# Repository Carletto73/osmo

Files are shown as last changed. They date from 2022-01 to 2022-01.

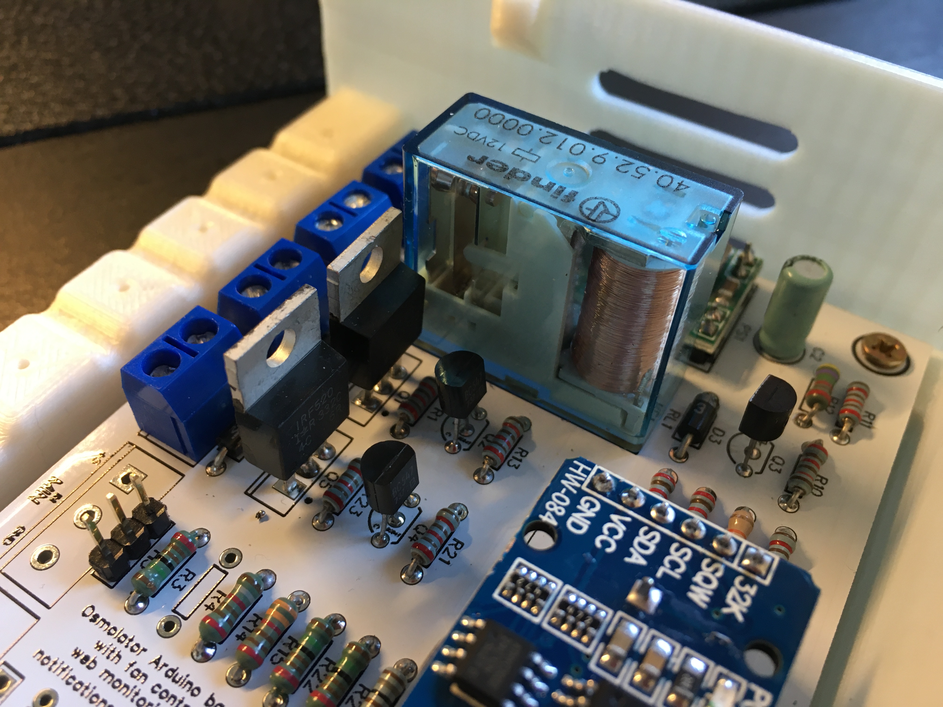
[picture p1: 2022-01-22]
assembly/IMG_1388.JPG

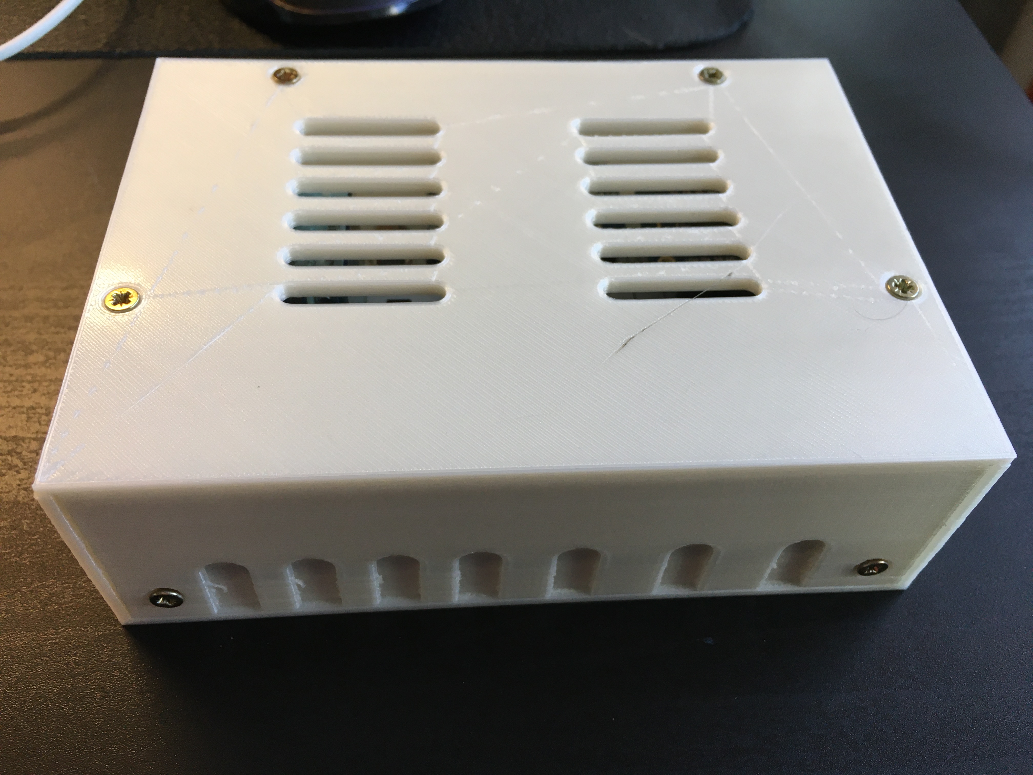
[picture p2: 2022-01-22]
assembly/IMG_1394.JPG

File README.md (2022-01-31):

# osmo
Osmolator for aquarium Arduino based



The typical osmolators are just a simple relay that feed the pump when the water level in the tank is low. This osmolator add several feature like:
1) web server to check the hystory of the pump activation
2) Telegram interface for settings and alarms
3) pump softstart and softstop
4) diagnostic of MIN and MAX level sensors
5) auto-diagnostic of power stadium inside the devise
6) temperature sensors and FAN output in case of water too hot







Web server for parametrization, status check, network credential change, ...



Telegram robot to check the osmolator status



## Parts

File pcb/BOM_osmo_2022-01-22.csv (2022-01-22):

ID | Name | Designator | Footprint | Quantity | Manufacturer Part | Manufacturer | Supplier | Supplier Part | Price
1 | M035MM | AUX,AUX,DS18B20,DS18B20,MIN,MIN | SCREWTERMINAL-5MM-3 | 6
2 | 100uF | C1,C1 | CAP_TH_6.3MM | 2
3 | 22uF | C2,C2,C3,C3 | CAP_TH_5MM | 4
4 | 1N4007 | D1,D2,D3,D4 | DO-41_BD2.4-L4.7-P8.70-D0.9-FD | 4 | 1N4007 | Yangzhou Yangjie Elec Tech | LCSC | C211605 | 0.025
5 | EM513 | D1,D2,D3,D4 | DO-41_BD2.4-L4.7-P8.70-D0.9-FD | 4 | 1N4007 | Yangzhou Yangjie Elec Tech | LCSC | C211605 | 0.025
6 | HDR1X5-M | EXP,EXP | HDR-TH_5P-P2.54-V-M | 2 | HDR1X5-M | null | LCSC | C9900001260
7 | M025MM | FAN,FAN,MAX,MAX,PUMP,PUMP,VIN,VIN | SCREWTERMINAL-5MM-2 | 8
8 | Header-Male-2.54_1x3 | H1,H1,H2,H2,H3,H3,H4,H4 | HDR-TH_3P-P2.54-V-M-1 | 8 | Header2.54mm 1*3P | BOOMELE | LCSC | C49257 | 0.017
9 | MP1584EN MODULE | PS1,PS1 | MP1584EN-MODULE | 2 | MP1584EN Module
10 | IRF540 | Q1,Q1,Q5,Q5 | TO-220-3_L10.0-W4.5-P2.54-L | 4 | IRF540ZP | VBsemi Elec | LCSC | C709597 | 1.149
11 | BC547 | Q2,Q2,Q4,Q4 | BC547B 01 [PCB] | 4 | BC547 | SHIVRAM | SHIVRAM | BC547
12 | 2N2222A | Q3,Q3 | NPN-2N2222A | 2 | 2N2222A | Mauser | LCSC | C358533 | 0.032
13 | 10k | R1,R5,R6,R7,R10,R11,R13,R21,R23 | R_AXIAL-0.3 | 9
14 | 12k | R1,R5,R6,R7,R10,R11,R13,R21,R23 | R_AXIAL-0.3 | 9
15 | 1k | R2,R3,R4,R9,R14,R17,R17,R18,R18,R19,R19,R22 | R_AXIAL-0.3 | 12
16 | 1k5 | R2,R3,R14,R22 | R_AXIAL-0.3 | 4
17 | not mount | R4 | R_AXIAL-0.3 | 1
18 | 47k | R8,R12,R12 | R_AXIAL-0.3 | 3
19 | 68k | R8 | R_AXIAL-0.3 | 1
20 | 1k8 | R9 | R_AXIAL-0.3 | 1
21 | 3k3 | R15,R15,R16,R16 | R_AXIAL-0.3 | 4
22 | 4k7 | R20,R20 | R_AXIAL-0.3 | 2
23 | 40.52.9.012.0000 | RL1,RL1 | FINDER-40.52 | 2 | New SchematicLib
24 | WEMOS_D1_MINI_PRO | U1,U1 | DIP-16_WEMOS_D1_MINI_PRO4 | 2 | Wemos_D1_mini_Pro4 | null | LCSC | C2837266
25 | RTC-DS3231-AT24C32 | U2,U2 | RTC-DS3231-AT24C32 | 2

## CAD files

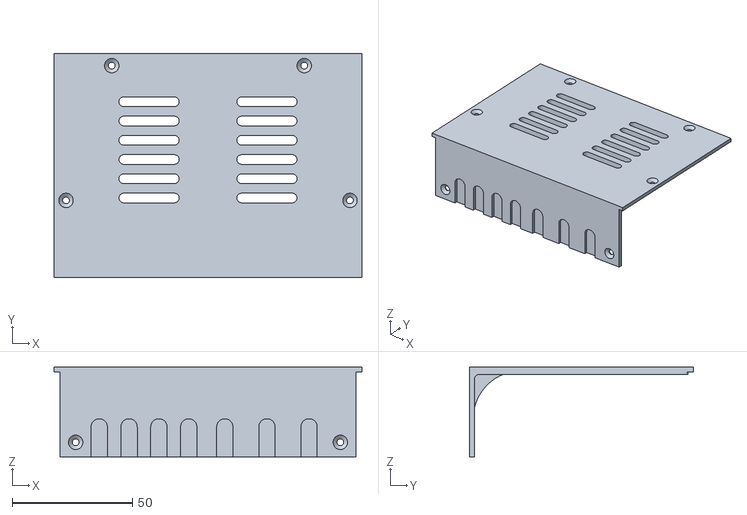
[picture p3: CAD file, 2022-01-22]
box/osmo_cover.stl
128.0 x 93.0 x 37.2

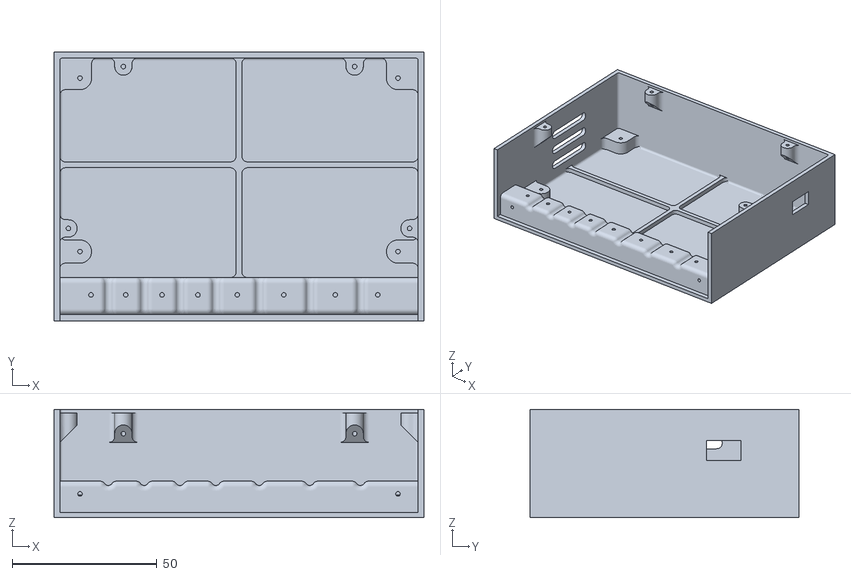
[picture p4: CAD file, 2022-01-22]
box/osmo_base.stl
128.0 x 93.0 x 37.4

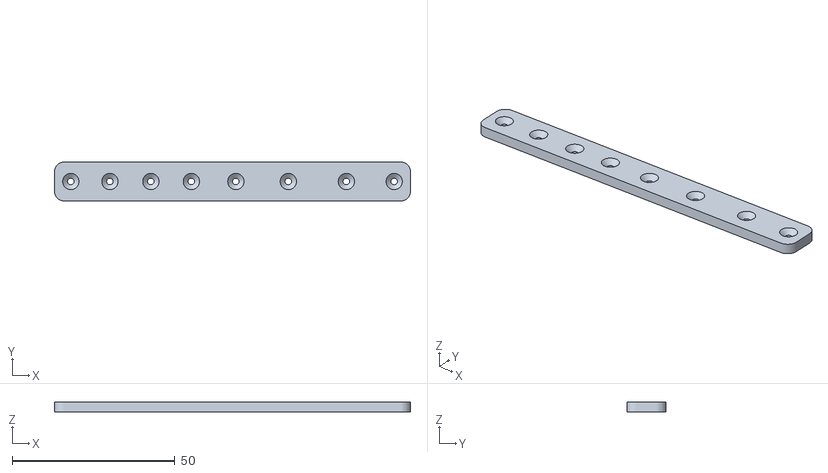
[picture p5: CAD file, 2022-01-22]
box/osmo_tpu.stl
109.2 x 12.0 x 3.00

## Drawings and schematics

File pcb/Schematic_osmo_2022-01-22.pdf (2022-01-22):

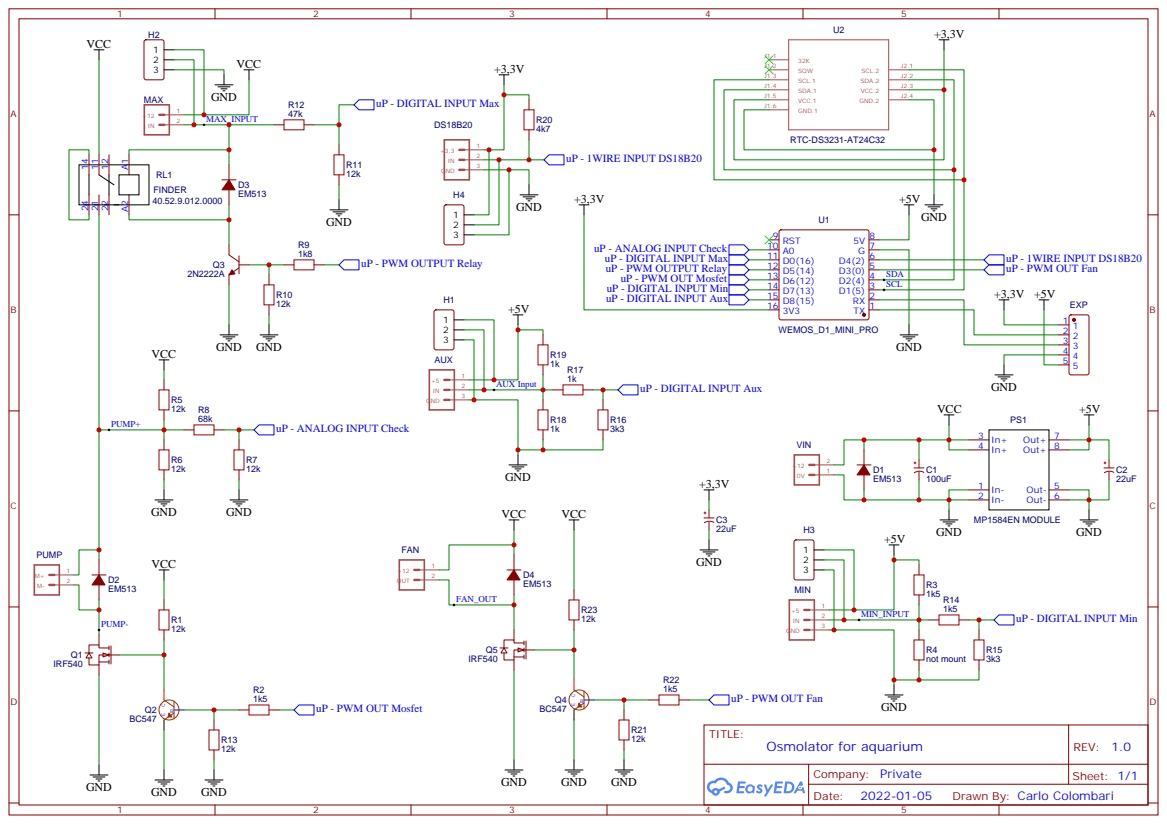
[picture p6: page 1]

uP - ANALOG INPUT Check
uP - DIGITAL INPUT Max
uP - PWM OUTPUT Relay
uP - PWM OUT Mosfet
uP - DIGITAL INPUT Min
uP - DIGITAL INPUT Aux

uP - 1WIRE INPUT DS18B20
uP - PWM OUT Fan

Drawn By: Carlo Colombari

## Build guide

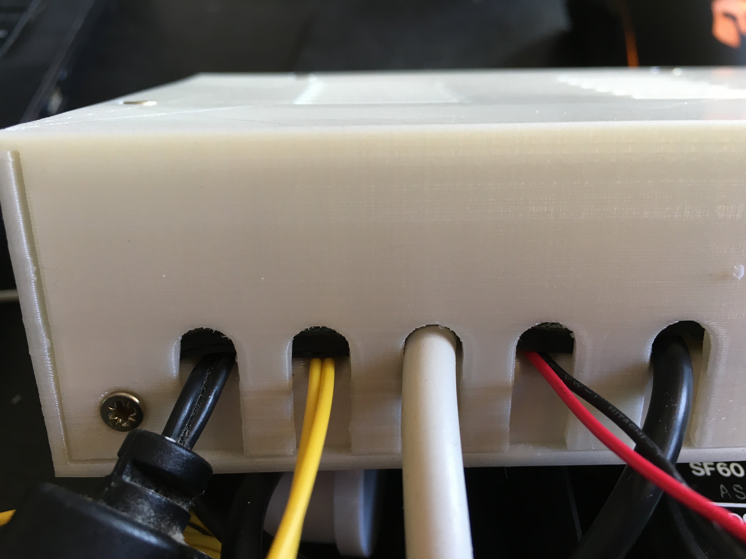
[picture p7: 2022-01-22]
assembly/IMG_1399.JPG

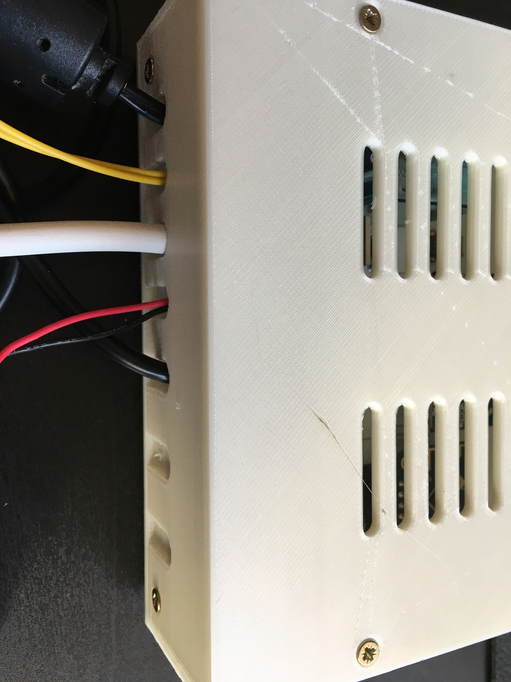
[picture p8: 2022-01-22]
assembly/IMG_1400.JPG

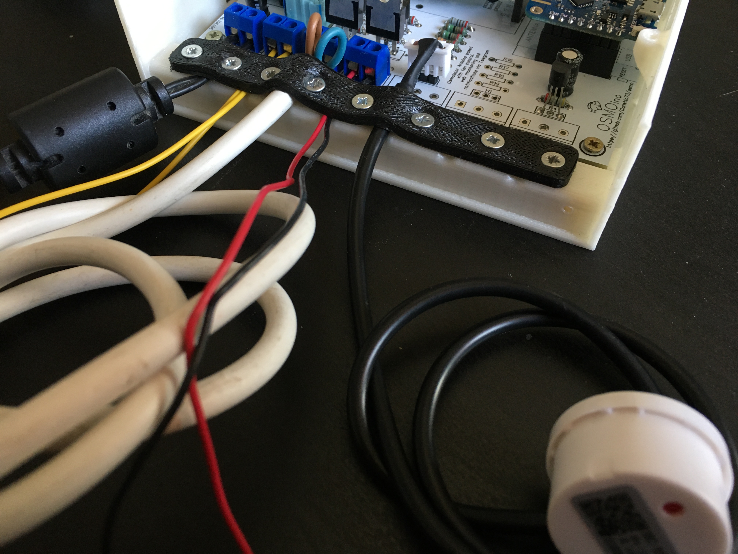
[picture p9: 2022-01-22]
assembly/IMG_1397.JPG

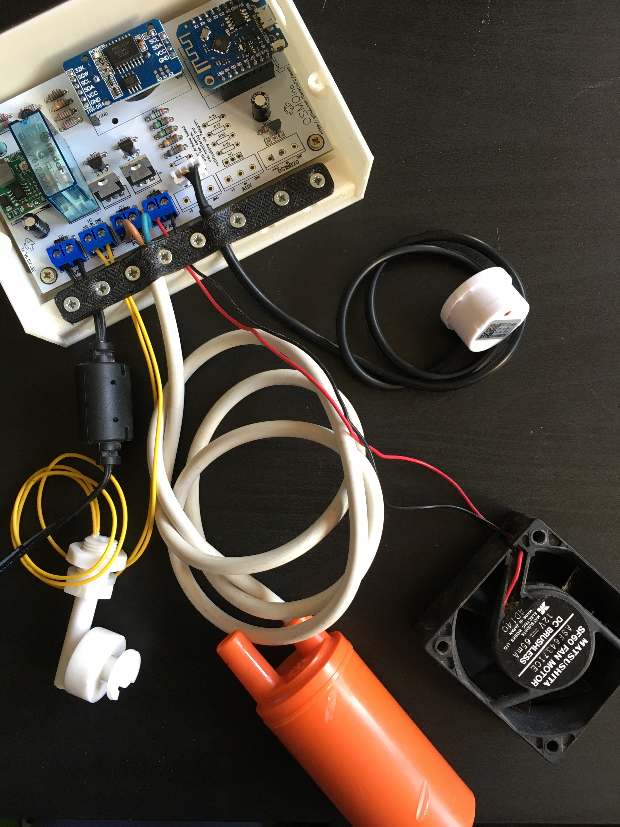
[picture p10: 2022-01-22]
assembly/IMG_1395.JPG

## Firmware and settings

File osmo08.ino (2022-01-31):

/*
  release 08: release candidate
*/

#include <ESP8266WiFi.h>
#include <WiFiClient.h>
#include <ESP8266WebServer.h>
#include <ESP8266mDNS.h>
#include <EEPROM.h>
#include <Arduino.h>
#include "AsyncTelegram.h"
#include <microDS3231.h>
#include <OneWire.h>
#include <DS18B20.h>
#include <AT24Cxx.h>

// EEPROM inside the DS3231 initialization
#define i2c_address 0x57
AT24Cxx eep(i2c_address, 32);

// OneWire and DS18B20 initialization
#define ONE_WIRE_BUS              2
OneWire oneWire(ONE_WIRE_BUS);
DS18B20 sensor(&oneWire);

// Created object for Telegram
AsyncTelegram myBot;

// Created object for RTC
MicroDS3231 rtc;

// Declaration
byte test;
byte state_releveling = 0;
byte pwm_pump = 255;
byte pwm_fan = 255;
byte pump_fault = 0;
byte last_second_start = 0;
byte last_minute_start = 0;
byte last_hour_start = 0;
byte last_day_start = 0;
byte last_month_start = 0;
byte last_year_start = 0;
byte last_dev_temperature_start = 0;
byte param_filt_max_level = 0;
byte param_filt_min_level = 0;
float param_temp_fan_activation = 0;
byte param_fan_hysteresis = 0; 
byte param_max_time_pump_on = 60;

int signal_percent[] = {0, 0, 0, 0, 0, 0, 4, 6, 8, 11, 13, 15, 17, 19, 21, 23, 26, 28, 30, 32, 34, 35, 37, 39, 41, 43, 45, 46, 48, 50, 52, 53, 55, 56, 58, 59, 61, 62, 64, 65, 67, 68, 69, 71, 72, 73, 75, 76, 77, 78, 79, 80, 81, 82, 83, 84, 85, 86, 87, 88, 89, 90, 90, 91, 92, 93, 93, 94, 95, 95, 96, 96, 97, 97, 98, 98, 99, 99, 99, 100, 100, 100, 100, 100, 100, 100, 100, 100, 100, 100, 100, 100, 100, 100, 100, 100, 100, 100, 100, 100};
String st;
float temperature_water;
unsigned long prev_overflow_time;
unsigned long prev_minimum_level_time;
unsigned long begin_time_timeout_pump;
unsigned long prev_state_releveling_time;
unsigned long prev_time_with_pump_stopped;
unsigned long duration_last_pumping;
bool water_overflow = true;
bool water_under_limit = false;
bool mosfet_closed = false;
bool relay_closed = false;
bool pump_timeout = false;
bool pump_stopped_in_previus_activation = true;
bool rtc_working = false;
bool pumping_ended_in_overflow = false;
bool telegram_unconnected;
bool connection_timeout;
bool request_change_account;
bool request_history;
bool request_parameter;
bool fan_switched_on = false;
bool request_preset_available = false;    

// E²PROM
// 0÷95 ID & PSW router
// 96÷159 Token telegram
// 160 pump_fault
// 161 param_filt_max_level
// 162 param_filt_min_level
// 163 param_temp_fan_activation (not float but 24°C + (value 163 * 0.1°C) )
// 164 param_fan_hysteresis
// 165 param_max_time_pump_on

#define OUTPUT_RELAY 14
#define OUTPUT_MOSFET 12
#define OUTPUT_FAN 0
#define ANALOG_INPUT_CHECK A0
#define INPUT_MAX_LEVEL 16
#define INPUT_MIN_LEVEL 13

// Create an instance of the server
// specify the port to listen on as an argument
ESP8266WebServer server(80);

// Main routine
void pump_manager()
{
  unsigned long current_time = millis();

  //Request if the temperature reading is available and launch a new reading
  if (sensor.isConversionComplete())
  {
    temperature_water = sensor.getTempC();  
    sensor.requestTemperatures();
  }

  // Filter on MAX level input
  if (digitalRead(INPUT_MAX_LEVEL))
  {
    if (current_time > (prev_overflow_time + (param_filt_max_level * 100))) // filter for max level
    {
      water_overflow = false;
    }
  }
  else
  {
    prev_overflow_time = current_time;
    water_overflow = true;
  }

  // Filter on MIN level input
  if (digitalRead(INPUT_MIN_LEVEL))
  {
    if (current_time > (prev_minimum_level_time + (param_filt_min_level * 100))) // filter for min level
    {
      water_under_limit = true;
    }
  }
  else
  {
    prev_minimum_level_time = current_time;
    water_under_limit = false;
  }

// These value are taken experimentally
  if (analogRead(ANALOG_INPUT_CHECK) < 175)
  {
    mosfet_closed = true;
    relay_closed = false;
  }
  else if (analogRead(ANALOG_INPUT_CHECK) > 525)
  {
    mosfet_closed = false;
    relay_closed = true;
  }
  else
  {
    mosfet_closed = false;
    relay_closed = false;
  }
  
// If is all right start the routine that feed check the hardware and starts the motor
  if(water_under_limit && !water_overflow && !pump_fault && pump_stopped_in_previus_activation)
  {
    switch (state_releveling)
    {
      case 0: // begin of pump phase
        if (rtc_working)
        {
          last_second_start = rtc.getSeconds();
          last_minute_start = rtc.getMinutes();
          last_hour_start = rtc.getHours();
          last_day_start = rtc.getDate();
          last_month_start = rtc.getMonth();
          last_year_start = rtc.getYear() % 100;
          last_dev_temperature_start = rtc.getTemperature();
          //stringHTML += String(rtc.getTemperatureFloat()).substring(0, 4);
        }
        else
        {
          last_second_start = 0;
          last_minute_start = 0;
          last_hour_start = 0;
          last_day_start = 1;
          last_month_start = 1;
          last_year_start = 20;
          last_dev_temperature_start = 0;
        }
        state_releveling = 1;
        prev_state_releveling_time = current_time;
        duration_last_pumping = 0;
        pumping_ended_in_overflow = false;
        break;
      case 1: // check if mosfet and relay are open
        if (current_time > (prev_state_releveling_time + 100))
        {
          prev_state_releveling_time = current_time;
          if (!mosfet_closed && !relay_closed)
          {
            state_releveling = 2;
          }
          else
          {
            if (relay_closed) 
            {
              pump_fault = 1;  // pump_fault = 1 >>> Relay stucked 
              EEPROM.write(160, pump_fault);
              EEPROM.commit();
            }
            if (mosfet_closed)
            {
              pump_fault = 2; // pump_fault = 2 >>> Mosfet in short-circuit
              EEPROM.write(160, pump_fault);
              EEPROM.commit();
            }
          }
        }
        break;
      case 2: // check if the mosfet works
        analogWrite(OUTPUT_MOSFET, 0); // Switch ON the mosfet
        if (current_time > (prev_state_releveling_time + 100))
        {
          prev_state_releveling_time = current_time;
          if (mosfet_closed)
          {
            analogWrite(OUTPUT_MOSFET, 255); // Switch OFF the mosfet
            state_releveling = 3;
          }
          else
          {
            pump_fault = 3; // pump_fault = 3 >>> Mosfet don't work
            EEPROM.write(160, pump_fault);
            EEPROM.commit();
          }
        }
        break;
      case 3: // delay
        if (current_time > (prev_state_releveling_time + 100))
        {
          prev_state_releveling_time = current_time;
          state_releveling = 4;
        }
        break;
      case 4: // check if the relay works
        digitalWrite(OUTPUT_RELAY, HIGH);
        if (current_time > (prev_state_releveling_time + 100))
        {
          prev_state_releveling_time = current_time;
          if (relay_closed)
          {
            state_releveling = 5;
          }
          else
          {
            pump_fault = 4; // pump_fault = 4 >>> Relay don't work
            EEPROM.write(160, pump_fault);
            EEPROM.commit();
          }
        }
        break;
      case 5: // soft-start pump
        prev_state_releveling_time = current_time;
        if (pwm_pump > 0)
        {
          pwm_pump--;
        }
        else
        {
          state_releveling = 6;
          begin_time_timeout_pump = current_time;
        }
        analogWrite(OUTPUT_MOSFET, pwm_pump); // 0=Switch ON / 255=Switch OFF
        break;
      case 6: // check_timeout
        prev_state_releveling_time = current_time;
        if (current_time > (begin_time_timeout_pump + (param_max_time_pump_on * 1000)))
        {
          pump_fault = 5; // pump_fault = 5 >>> Timeout (max time reach)
          EEPROM.write(160, pump_fault);
          EEPROM.commit();
        }
        break;
    }
  }
  else
  {
    if (pwm_pump < 255)
    {
      if (pwm_pump < 255) pwm_pump++;
      if (pwm_pump < 255) pwm_pump++;
      if (pwm_pump < 255) pwm_pump++;
      prev_state_releveling_time = current_time;
      pump_stopped_in_previus_activation = false;
      state_releveling = 7; // soft-stop pump
      if (water_overflow)
      {
        pwm_pump = 255;
        pumping_ended_in_overflow = true;
      }
    }
    else
    {
      if (current_time > (prev_state_releveling_time + 200))
      {
        digitalWrite(OUTPUT_RELAY, LOW);
        pump_stopped_in_previus_activation = true;
        if (state_releveling != 0)
        {
          state_releveling = 0;
          for (int i = 0 ; i <= 100 ; i++)
          {
            if (eep.read(i * 16) == 0)
            {
              Serial.print("Indice memoria: ");
              Serial.println(i);
              int temp = temperature_water * 100;
              eep.write((i * 16) + 0, last_year_start);                     // year
              eep.write((i * 16) + 1, last_month_start);                    // month
              eep.write((i * 16) + 2, last_day_start);                      // day
              eep.write((i * 16) + 3, last_hour_start);                     // hour
              eep.write((i * 16) + 4, last_minute_start);                   // minute
              eep.write((i * 16) + 5, last_second_start);                   // second
              eep.write((i * 16) + 6, duration_last_pumping / 1000);        // duration second
              eep.write((i * 16) + 7, (duration_last_pumping % 1000) / 10); // duration cent/second
              eep.write((i * 16) + 8, pumping_ended_in_overflow);           // overflow
              eep.write((i * 16) + 9, pump_fault);                          // fault
              eep.write((i * 16) + 10, last_dev_temperature_start);         // temperature device
              eep.write((i * 16) + 11, temp / 100);                         // temperature water
              eep.write((i * 16) + 12, temp % 100);                         // temperature water decimal
              eep.write((i * 16) + 13, 0);                                  // free
              eep.write((i * 16) + 14, 0);                                  // free
              eep.write((i * 16) + 15, 0);                                  // free
              if (i != 100)
              {
                for (int j = 0 ; j < 16 ; j++)
                {
                  eep.write(((i + 1) * 16) + j, 0); // cancel next slot
                }
              }
              else
              {
                for (int j = 0 ; j < 16 ; j++)
                {
                  eep.write(j, 0); // cancel next slot
                }
              }
              break;
            }
          }
        }
      }
    }
    analogWrite(OUTPUT_MOSFET, pwm_pump); // 0=Switch ON / 255=Switch OFF
  }
  if (pwm_pump != 255)
  {
    duration_last_pumping = current_time - prev_time_with_pump_stopped;
  }
  else
  {
    prev_time_with_pump_stopped = current_time;
  }

// FAN manager
  float temp_float = param_fan_hysteresis / 10.0;
  if (temperature_water >= param_temp_fan_activation)
  {
    digitalWrite(OUTPUT_FAN, LOW); // inverted
    fan_switched_on = true;
  }
  else if (temperature_water < param_temp_fan_activation - temp_float)
  {
    digitalWrite(OUTPUT_FAN, HIGH); // inverted
    fan_switched_on = false;
  }
}

void setup()
{

  // Set the output
  pinMode(LED_BUILTIN, OUTPUT);
  pinMode(OUTPUT_RELAY, OUTPUT);
  pinMode(OUTPUT_MOSFET, OUTPUT);
  pinMode(OUTPUT_FAN, OUTPUT);
  pinMode(INPUT_MAX_LEVEL, INPUT);
  pinMode(INPUT_MIN_LEVEL, INPUT);
  pinMode(ANALOG_INPUT_CHECK, INPUT);
  digitalWrite(LED_BUILTIN, 0);
  digitalWrite(OUTPUT_RELAY, LOW);
  digitalWrite(OUTPUT_MOSFET, HIGH); // inverted
  digitalWrite(OUTPUT_FAN, HIGH); // inverted

  // Opening serial monitor
  Serial.begin(115200);
  delay(100);
  Serial.println();
  Serial.println();
  Serial.println();
  Serial.println();
  Serial.println();
  Serial.println(F("Start Program"));

  // Preset RTC in case of lostPower
  if (rtc.lostPower())
  {
    rtc.setTime(BUILD_SEC, BUILD_MIN, BUILD_HOUR, BUILD_DAY, BUILD_MONTH, BUILD_YEAR);
    Serial.println("DS3231 presetted");
  }

  // Disconnect current wifi
  WiFi.disconnect();

  // Initialasing EEPROM
  EEPROM.begin(512);

  // Check the RTC connection
  if (!rtc.begin())
  {
    rtc_working = false;
    Serial.println("DS3231 not found");
  }
  else
  {
    rtc_working = true;
    Serial.print("DS3231 found ");
    Serial.print(" Date ");
    Serial.print(rtc.getDate());
    Serial.print("/");
    Serial.print(rtc.getMonth());
    Serial.print(" Hour ");
    Serial.print(rtc.getHours());
    Serial.print(":");
    Serial.print(rtc.getMinutes());
    Serial.print(":");
    Serial.println(rtc.getSeconds());
  }

  // Initialasing DS18B20
  sensor.begin();
  sensor.requestTemperatures();
  
  // Read SSID and Password from EEPROM
  Serial.print(F("    SSID stored in EEPROM: "));
  String esid;
  for (byte i = 0; i < 32; ++i)
  {
    esid += char(EEPROM.read(i));
  }
  esid = esid.c_str();
  Serial.println(esid);

  Serial.print(F("PASSWORD stored in EEPROM: "));
  String epass = "";
  for (int i = 32; i < 96; ++i)
  {
    epass += char(EEPROM.read(i));
  }
  epass = epass.c_str();
  //Serial.println(epass);
  Serial.println("******************************");

  Serial.print(F("   TOKEN stored in EEPROM: "));
  char* token = "1234567890:ABCDEFGHIJKLMNOPQRSTUVWXYZABCDEFGHI";     // REPLACE myToken WITH YOUR TELEGRAM BOT TOKEN
  for (int i = 96; i < 160; ++i)
  {
    token[i - 96] = char(EEPROM.read(i));
  }
  Serial.println(token);

  // Read the parameters on EEPROM
  pump_fault = EEPROM.read(160);
  param_filt_max_level = EEPROM.read(161);
  param_filt_min_level = EEPROM.read(162);
  param_temp_fan_activation = 24 + (EEPROM.read(163) * 0.1);
  param_fan_hysteresis = EEPROM.read(164);
  param_max_time_pump_on = EEPROM.read (165);

  // Connect to WiFi network with 60 seconds of timeout
  Serial.print(F("Connecting to "));
  Serial.println(esid);
  WiFi.setAutoConnect(true);   
  WiFi.mode(WIFI_STA);
  WiFi.begin(esid, epass);

  unsigned long previousMillis = millis();
  while ((WiFi.status() != WL_CONNECTED) && (millis() < 60000))
  {
    if (millis() > previousMillis + 250)
    {
      Serial.print(F("."));
      previousMillis = millis();
    }
  }
  // connection router timeout
  if (millis() >= 60000)
  {
    Serial.println();
    Serial.println(F("Wifi timeout. WiFi NOT connected"));
    connection_timeout = true;

    // Start hotspot
    Serial.println("Server started as HotSpot after timeout (allow to change SSID and PASSWORD)");

    // Before to start the hotspot are checked the networks available
    WiFi.mode(WIFI_STA);
    WiFi.disconnect();
    delay(100);
    int n = WiFi.scanNetworks();
    Serial.println(F("Scan done"));
    if (n == 0)
    {
      Serial.println(F("No networks found"));
      st = "<ol><li>No networks found</li></ol>";
    }
    else
    {
      Serial.print(n);
      Serial.println(F(" networks found"));
      st = F("<ol>");
      for (int i = 0; i < n; ++i)
      {
        // Print SSID and RSSI for each network found
        Serial.print(i + 1);
        Serial.print(F(": "));
        Serial.print(WiFi.SSID(i));
        Serial.print(F(" ("));
        Serial.print(WiFi.RSSI(i));
        Serial.print(F("dB) ("));
        Serial.print(signal_percent[100 + WiFi.RSSI(i)]);
        Serial.print(F("%)"));
        Serial.println((WiFi.encryptionType(i) == ENC_TYPE_NONE) ? " Not protect" : " Protect");
        st += F("<li>");
        st += WiFi.SSID(i);
        st += F(" (");
        st += WiFi.RSSI(i);
        st += F("dB) (");
        st += signal_percent[100 + WiFi.RSSI(i)];
        st += F("%)");
        st += (WiFi.encryptionType(i) == ENC_TYPE_NONE) ? " " : " *";
        st += F("</li>");
        delay(10);
      }
      st += F("</ol>");
      st += F("(*) Protected</br>");
      Serial.println("");
    }

    // Opening of hotspot
    delay(200);
    WiFi.softAP("Osmo", "Osmolator");
    Serial.println("Initializing_softap_for_wifi credentials_modification");
    server.onNotFound(handleWebPage);
    
    // CreateWebServer();
    server.begin();

    // Preset timers
    prev_overflow_time = millis();
    prev_minimum_level_time = prev_overflow_time;
    begin_time_timeout_pump = prev_overflow_time;
    prev_state_releveling_time = prev_overflow_time;
    prev_time_with_pump_stopped = prev_overflow_time;
    prev_time_with_pump_stopped = duration_last_pumping;
  }
  // connection on time
  else
  {
    Serial.println();
    Serial.println(F("WiFi connected"));
    digitalWrite(LED_BUILTIN, 1);
    // set the local DNS name
    if (MDNS.begin("osmo"))
    {
      Serial.println("MDNS responder started.      HTTP://osmo.local/");
    }
    // for all web request it calls the handleWebPage function
    server.onNotFound(handleWebPage);
    // Start the server
    server.begin();
    Serial.println(F("Server started"));

    // Print the IP address
    Serial.println(WiFi.localIP());
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
void loop()
{
  server.handleClient();
  if (connection_timeout == false) {MDNS.update();}
  if ((telegram_unconnected == false) && (connection_timeout == false)) {handleTelegram();}
  pump_manager();
  delay(5); // this delay blocking is realy need. removing it web and telegram not work
}

void handleWebPage()
{
  // Read the request
  String req = server.uri();
  int history_page;

  if (req == "/favicon.ico") return;
 
  test += 1;

  // check if was required a fault reset
  if (req.indexOf(F("/reset")) != -1)
  {
    pump_fault = 0;    
    EEPROM.write(160, pump_fault);
    EEPROM.commit();
  }

  // check if was required a credential network change
  if (req.indexOf(F("/account")) != -1)
  {
    request_change_account = true;    
  }
  else
  {
    request_change_account = false;    
  }
  
  // check if was required a history activation page
  if (req.indexOf(F("/history")) != -1)
  {
    request_history = true;
    history_page = server.arg(0).toInt();
  }
  else
  {
    request_history = false;    
  }

  // check if was required a preset parameters
  if (req.indexOf(F("/preset")) != -1)
  {
    if (request_preset_available)
    {
      EEPROM.write(161, 10);
      EEPROM.write(162, 10);
      EEPROM.write(163, 30);
      EEPROM.write(164, 10);
      EEPROM.write(165, 60);
      EEPROM.commit();
      param_filt_min_level = 10;
      param_filt_max_level = 10;
      param_temp_fan_activation = 24 + (30 * 0.1);
      param_fan_hysteresis = 10;
      param_max_time_pump_on = 60;
      for (int i = 0 ; i <= 1616 ; i++)
      {
        eep.write(i, 0);
      }
    }
    request_preset_available = false; 
  }
  else
  {
    request_preset_available = true;    
  }

  // check if was required a parameters change
  if (req.indexOf(F("/parameter")) != -1)
  {
    request_parameter = true;
    if (server.arg(0).length() > 0)
    {
      param_filt_min_level = server.arg(0).toInt();
      param_filt_max_level = server.arg(1).toInt();
      param_temp_fan_activation = 24 + (server.arg(2).toInt() * 0.1);
      param_fan_hysteresis = server.arg(3).toInt();
      param_max_time_pump_on = server.arg(4).toInt();
      EEPROM.write(161, param_filt_max_level);
      EEPROM.write(162, param_filt_min_level);
      EEPROM.write(163, server.arg(2).toInt());
      EEPROM.write(164, param_fan_hysteresis);
      EEPROM.write(165, param_max_time_pump_on);
      EEPROM.commit();
    }
  }
  else
  {
    request_parameter = false;    
  }

  // check if was required a data change
  if (req.indexOf(F("/date")) != -1)
  {
    rtc.setTime(0, server.arg(4).toInt(), server.arg(3).toInt(), server.arg(0).toInt(), server.arg(1).toInt(), server.arg(2).toInt());
    Serial.println("Changed hour");
  }

  // check if was required a setting change
  if (req.indexOf(F("/setting")) != -1)
  {
    String qsid = server.arg(0);
    String qpass = server.arg(1);
    String qtoken = server.arg(2);
    Serial.println("");
    if (qsid.length() > 0 && qpass.length() > 0)
    {
      Serial.println(F("Clearing eeprom"));
      for (int i = 0; i < 96; ++i)
      {
        EEPROM.write(i, 0);
      }
      Serial.println(qsid);
      Serial.println(qpass);
      Serial.println(F("Writing eeprom SSID:"));
      for (int i = 0; i < qsid.length(); ++i)
      {
        EEPROM.write(i, qsid[i]);
      }
      Serial.println(F("Writing eeprom PASSWORD:"));
      for (int i = 0; i < qpass.length(); ++i)
      {
        EEPROM.write(32 + i, qpass[i]);
      }
      EEPROM.commit();
    }
  
    if (qtoken.length() > 0)
    {
      Serial.println(F("Clearing eeprom"));
      for (int i = 96; i < 160; ++i)
      {
        EEPROM.write(i, 0);
      }
      Serial.println(qtoken);
      Serial.println(F("Writing eeprom TOKEN:"));
      for (int i = 0; i < qtoken.length(); ++i)
      {
        EEPROM.write(96 + i, qtoken[i]);
      }
      EEPROM.commit();
     }

    // Disconnect current wifi in case of parameter changed
    if ((qsid.length() > 0 && qpass.length() > 0) || (qtoken.length() > 0))
    {
      WiFi.disconnect();
      ESP.reset();
    }
  }

  // Main web page
  String stringHTML = F("");
  if (!connection_timeout && !request_change_account && !request_history && !request_parameter)
  {
    stringHTML += F("<html>");
    stringHTML += F("<head>");
    if (req == "/") stringHTML += F("<meta http-equiv=\"refresh\" content=\"3\">");
    stringHTML += F("</head>");
    stringHTML += F("<body>");
    stringHTML += F("<table style=\"border-collapse: collapse; width: 100%;\" border=\"1\">");
    stringHTML += F("<tbody>");
    stringHTML += F("<tr>");
    stringHTML += F("<td style=\"width: 100%; text-align: center; font-size: 36pt;\"><strong><font color=\"red\"><a title=\"refresh\" style=\"text-decoration: none\" href=\"http:/\">OSMOLATOR</a></font></strong></td>");
    stringHTML += F("</tr>");
    stringHTML += F("<tr>");
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
